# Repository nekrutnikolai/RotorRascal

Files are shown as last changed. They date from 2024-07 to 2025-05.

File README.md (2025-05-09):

## Final Project Report

<p align="center">
    Final Project Website for ECE 5730<br>
    Bryan Peters (bmp85), Martin Kostal (mk2378), Nikolai Nekrutenko (nan34)
</p>

<p align="center">
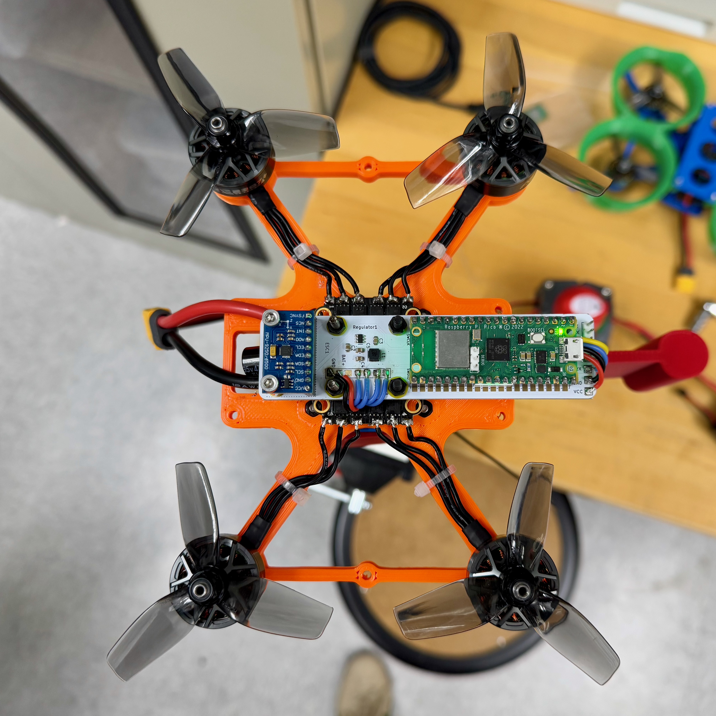
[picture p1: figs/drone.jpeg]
Drone
    
</p>

### Project Introduction

#### One sentence "sound bite" that describes your project
    
We built and implemented PID control on a Pico-powered quadcopter to hover on a gimbal stand with throttle input from a controller. 

#### A summary of what you did and why

We built a functional quadcopter system powered by a Raspberry Pi Pico, implementing a full PID-based flight controller from scratch to enable stable hover on a custom gimbal stand. Our goal was to design a hands-on, educational drone platform that could be integrated into ECE and MAE course curricula, allowing students to work directly with embedded systems, control theory, and dynamics. Starting from a partially developed hardware prototype and minimal software, we developed our own PID control logic, tuned it through extensive testing, and integrated radio-based throttle control. This project not only demonstrated our understanding of embedded flight control, but also laid the groundwork for a low-cost, reproducible drone platform for future student use.

### High level design

#### Rationale and sources of your project idea

Bryan, Martin and I enjoy drones and quadcopters, we thought it would be a neat idea to develop a somewhat functioning flight controller to control the drone with an onboard IMU for orientation data, an external remote to set the throttle position, and an electronic speed controller (ESC). 
    
Nikolai is a part of the Motion Studio "Drone Squad" advised by Dr. Beatriz Asfora which was involved in the creating of this final project idea. Out of the Drone Squad there was already a prototype developed by Deemo Chen with a PCB integrating an IMU and Pi Pico along with a skeleton of code on how to control each PWM ESC channel.

The long-term objective of this project is to support the integration of these Pico-based drones made from 3D printed components into ECE and MAE courses. For instance, these drones could be integrated in the ECE microcontrollers curriculum and the students could work on code developing/tuning a PID controller. Or, for a MAE dynamics course, the students could use these drones for dynamics modelling.

#### Background math

The effects of a $P$, $I$ and $D$ terms are well know. If we think of controlling the mass in a spring-mass-dashpot system, the $P$ term acts like increasing the stiffness of the spring, whereas the $D$ term effectively adds damping to the system. An $I$ term in general achieves the desirable property of having zero steady state. 

Even though our system is not a spring-mass-dashpot system, we can still keep in mind the above intuitive properties of each of the three terms of a PID controller. 
    
We ended up using the same set of three $P$, $I$, $D$ coefficients for controlling the pitch and the roll angle, and a different set of three $P$, $I$, $D$ coefficients for the yaw angle. Therefore, $6$ in total.

We did not do any modelling of the drone ("plant") dynamics, and did the tuning by trial and error. With more time, we would obtain the equations of motion and linearize about the desired hover position. We would get a linear set of equations, keeping in mind that we should include a model of noise in the measurements obtained from the IMU. There would be two standard approaches we could have taken: either design the controller using the state-space approach, or frequency design. Preceeding each of these two approaches, we would first have to obtain the dynamical equations of motion from Newton's second law and then linearize them about the desired hover position. 

Getting the dynamical equations of motion would have been non-trivial for several reasons, and was not achievable in the allocated time for this project. First of all, we would have to obtain the center of mass and tensor of inertia with respect to the gimbal, treating the drone as a rigid body. This could have been obtained from a CAD assembly, but only approximately - due to the geometry of $3D$ printed layers, see linked files for the individual parts. (Furthermore, the chip itself, the IMU, the wiring, the battery would all change these quantities, and indicate why it would have been really hard to obtain at least a reasonable model of the dynamics.) Second of all, the friction at the gimbal on the frame of the drone and the pull of the cables would have to be modelled. The thrust of the propellers in terms of the duty cycle of our PWM control signal supplied to the motors would be obtained from the documentation of the propeller's manufacturer. We should keep in mind that the gimbal support was not located under the center of mass. 

#### Logical structure
   
1. Initialize radio and sensors
2. Calibrate ESCs and Gyro
3. Initialize serial PID tuning interface
4. Wait for arm signal from controller
    1. Erase all store PID values -- effectively reset controls
5. Spin up motors to minimum throttle and begin executing PID loop
6. Continue executing PID loop until disarm

<p align="center">
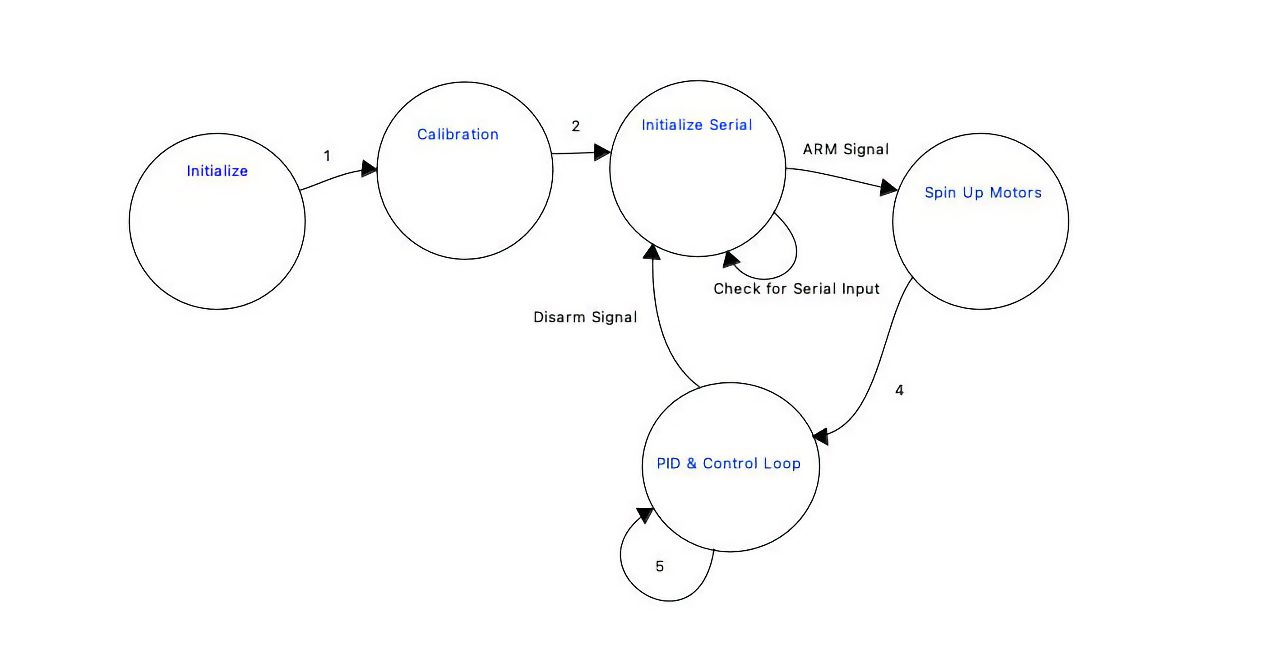
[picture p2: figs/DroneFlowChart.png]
DroneChart
    
</p>

#### Hardware/software tradeoffs
    
- **PID loop speed:** Since the drone is a complicated, unstable system with 4 motors and 6 degrees of freedom, it is vital to have a fast control loop. From our testing and with lab 3, we found a value of 1kHz to work well. Compared to lab 3, we need to be computing the PID terms for 3 axes as opposed to a single PID axis. Those three axes are pitch, roll, and yaw. Pitch and roll have the same PID parameters and yaw has different PID parameters that will be discussed later in this section. 

- **Pico W:** The Pico W was used to allow future expansion of wireless capabilities. Future work could involve developing a web server that hosts an interactive PID tuning interface where students in courses could drag sliders and visualize the gyro output and controller output to see the performance of the PID developed or the drone modelled.

- **Controlling 4 Motors:** The PWM needs to be computed for each of the 4 motors, as opposed to a single axis like in lab 3, which takes more time to compute. This point is combined with the previous point made above, leading to significantly more computation involved. Essentially, 6 (PID terms) x 3 (axes) x 4 (motors) = 64 times the amount of computation relative to lab 3 since that lab had 1 axis and 1 motor. Additionally, changing the motor output has effects on the physical system, where changing the motor speed induces a torque on the drone, affecting the yaw axis, which will be discussed in the next section.

- **Yaw Compensation:** Since the drone is a physical system, we had to take into account physics for our software development and development. The quick and dirty solution that we came up with was having different PID weights for the yaw axis as opposed to the pitch and roll axes. For instance, the D term had to be greatly reduced as so the yaw compensation would not fight the other axes and enter an unstable jittery mess.

- **Long-Term Gyro Drift:** Gyro drift could have an effect on the longer-term characteristics in the minute to hour timescales. This is not much of a concern, however, as the drone only has battery life for 5 minutes at most due to the extreme power draw of flight. We implemented the gyro to calibrate everytime a battery is plugged in, so the drone must be set level.

#### Discuss existing patents, copyrights, and trademarks which are relevant to your project.

There are no existing patents, copyrights, and trademarks which are relevant to our project.

### Program/hardware design

#### Program details. What parts were tricky to write?

The skeleton of code we started from was unnecessarily complicated, so our biggest challenge was discovering how the actual control algorithms and peripheral interfaces were implemented. The code for the radio interface was reverse-engineered based on the serial string received from the controller. Although that was straightforward, it was far less straightforward to implement pitch, roll, and yaw control from the controller to the rest of the code. Hence, we stuck with throttle and arm only. From there, we scrapped his PID control as it was unfinished and did not work and wrote our own. This has its own challenges as we are implementing it on a quadcopter with four motors. One really important thing that we realized early was that the physical model for how yaw is controlled is extremely different from how pitch and roll is controlled. This means we needed separate coefficients for yaw PID and pitch/roll PID. To implement this, we simply compute the PID values, then apply the coefficients separately in the motor mixing calculations. 

The code has the following structure:

```
RotorRascals
├── main.c                  # Entry point, initializes hardware and control loop
├── lib/
│   ├── Control/
│   │   ├── controller.c       # PID controller logic
│   │   └── controller.h
│   ├── ESC/
│   │   ├── esc.c              # Motor PWM control
│   │   └── esc.h
│   ├── Filter/
│   │   ├── leaky_LP.c         # Leaky low-pass filter
│   │   └── leaky_LP.h
│   ├── MPU9250/
│   │   ├── mpu9250.c          # IMU driver
│   │   └── mpu9250.h
│   ├── Radio/
│   │   ├── radio.c            # UART radio input parsing
│   │   └── radio.h
├── include/
│   ├── config.h               # System-wide configuration macros
│   └── pins.h                 # Pin definitions
├── utils/
│   └── math_utils.c/h         # Optional math helpers
├── Makefile or CMakeLists    # Build system configuration
```
  
#### Hardware details -- Could someone else build this based on what you have written?

Below is a diagram showcasing the drone components

<p align="center">
    DroneLabelled
</p>

The drone 3D printable files can be found at the following link:
1. DIYDrone Frame with Motor Holes:
https://cad.onshape.com/documents/d38aab018657bf04d68fdbe6/w/71b7a7a8d496a9da1491b
bbb/e/70127a797fc69afda087e221
2. DIYDrone (Jackson & Dylan) Guards:
https://cad.onshape.com/documents/7de229710a5769dcea70d33f/w/a361731c2e298d2c6e283
035/e/6aab78923736995bb8b96cf8
3. DIYDrone Gimbal Interfacer:
https://cad.onshape.com/documents/8b853f430eb67b22ed155352/w/298f6506e82bca0de68ad
df6/e/2c12097c2bd1bacce00dfebb?renderMode=0&uiState=680d8b0e72d068090b086e62
4. Drone Gimbal Mount & Gimbal Drone Spacer:
https://cad.onshape.com/documents/e9f49230253cb2ceb026b522/w/5f775122fa42329de5afc46
6/e/d2d7e1e364a8d0e3d6eb7b74

The drone build guide can be found at the following links:
1. Frame 3D printing guide: https://github.com/cornellmotionstudio/DIYDrone/wiki/Frame
2. Guards 3D priting guide: https://github.com/cornellmotionstudio/DIYDrone/wiki/Guards
3. Mechanical assembly guide: https://github.com/cornellmotionstudio/QuadPopUp/wiki/Part-1:-Build-Your-Quadcopter 
4. Electrical assembly/Pico software guide: https://github.com/cornellmotionstudio/JacksonDronev2/wiki

To get up and running with the code and Pico build environment:

Clone the project
``` bash
git clone https://github.com/nekrutnikolai/RotorRascal.git
```

Go to the software dir.
``` bash
cd RotorRascal && cd software
```

Build the project
``` bash
./builder
```

Below is a bill of materials will all the parts necessary to build the drone and get up and running

Table 1: Drone components

| **Component** | **Part Description** | **Estimated Price** |
|---|---|---|
| **Frame** | 3D Printed | $3-5 in filament |
| **Motors** | 2306 brushless motors, 1700–2500KV | $15–$30 each |
| **ESC (4-in-1)** | 4-in-1 ESC, 30–60A, DShot600 support | $40–$80 |
| **Propellers** | 3" tri-blade props | $3–$6 per set |
| **Radio Receiver (Rx)**| ELRS protocol receiver | $15–$30 |
| **Battery** | 4S LiPo, 1300–1800mAh | $25–$50 |

Table 2: Drone accessories

| **Component** | **Part Description** | **Estimated Price** |
|---|---|---|
| **Transmitter (Tx)** | Radiomaster Boxer ELRS RC controller | $100–$150 |
| **Battery Charger** | LiPo balance charger (AC/DC or DC only) | $40–$100 |

#### Be sure to specifically reference any design or code you used from someone else
    
We referenced the design and code found at the following repository: https://github.com/cornellmotionstudio/JacksonDronev2

### Tuning the drone PID's

Tuning the PIDs on a quadcopter is not the easiest task when it comes to a PID loop that you wrote yourself, on hardware that you also built yourself. It's especially difficult because there is no advice from other people that have experienced the issues. It boils down to a raw understanding of the physical model and the code at play. With our particular situation, the most difficult thing was trying to understand what was due to the gyro or if the issues were being caused by dynamics between the pitch and roll competing with yaw correction. Due to the physical model of a quadcopter, if a correction is made to any motor, it affects yaw, therefore inducing a yaw error that requires correction. Finding a starting point that did not have an oscillatory loop between the pitch/roll axis and the yaw axis was a challenge, but in the end, we were able to find a good starting point PIDs.

Table 3: Initial PID values

| Axis | Kp  | Ki | Kd |
|---|-----|---|---|
| Roll/Pitch  | 4.5 | 0.4  | 0.08  |
| Yaw | 3.0 | 0.25 | 0.015 |

Continuing with our tuning, we were able to find really good PID values that resulted in an ability to react really well to outside stimuli, hold level quite well, and correct for new changes in center of gravity on the drone. The biggest challenge is finding a set of PIDs that works well through the whole throttle range; however, though this should not be the case unless we are amplifying noise or vibration caused by different throttle positions in our accelerometer measurements. Something we did still experience regardless of the amount of tuning done was a continuous angle error that varied with time; it almost appeared to be steady-state error that would then be corrected by the I term, which led us down some tuning rabbit holes in attempts to fix it. However, we believe now that it is actually drift occurring through our complimentary filter, and given more time, I believe we would have been able to correct this issue. Coming to this conclusion was based on testing with a solid offset that would need to be corrected by the I term, which did occur and namely occurred much faster than the correction to this drift. Additionally, testing our P term by tapping different points to induce an angle error and observing how quickly the drone corrected these errors indicated that whatever this drift was, it was being ignored by the PID loop. Testing PIDs was done purely on a custom-designed stand designed by Nikolai. The stand allows the drone to move along the pitch, roll, yaw, and vertical axis. Meaning we can simulate a hover that is restricted in translational movement. Using this stand with a power cable and a USB cable dangling from opposite ends of the drone, we are able to safely test indoors despite the high chance of unstable flight. 

Table 4: Final PID values that we found to work best:

| Axis | Kp  | Ki | Kd |
|---|-----|---|---|
| Roll/Pitch  | 20.0 | 2.0  | 1.5  |
| Yaw | 3.0 | 0.25 | 0.015 |

### Results of the design

#### Any and all test data, scope traces, waveforms, etc

We tested the drone primarily on a custom-designed gimbal stand, which allowed safe experimentation of all rotational degrees of freedom (roll, pitch, yaw) and limited vertical movement. This setup enabled us to analyze hover stability, responsiveness, and overall system behavior under controlled conditions.

We evaluated PID response by:
- Applying known disturbances (e.g., tapping the frame) and observing response.
- Introducing sudden changes in throttle and analyzing recovery behavior.
- Monitoring gyro outputs in real time via serial logging.

Through this process, we fine-tuned the PID constants as shown in Table 4. 

Unfortunately, due to the 1kHz speed of the PID loop, we were unable to plot the data in real time without a noticeable reduction in performance.

#### Speed of execution (hesitation, flicker, interactiveness, concurrency)

The control loop was executed at **1 kHz**, which allowed timely updates and stable feedback. This speed was chosen based on earlier experimentation and provided a good balance between performance and computational headroom on the Pi Pico. There was **no observable hesitation or lag**, and the drone maintained high responsiveness to throttle changes and physical disturbances.

#### Accuracy (numeric, music frequencies, video signal timing, etc)

The orientation estimation was reasonably accurate for short time scales (under 2–3 minutes), with minor long-term drift observed due to IMU noise and limitations of the complementary filter. Control accuracy was sufficient to maintain a level hover and reject disturbances, though we noticed yaw compensation would lag slightly under certain conditions due to cross-axis coupling as a result of torque induced by the drone.

#### How you enforced safety in the design

Safety was a top priority throughout this project. The following measures were implemented:

- Test stand: Limited movement to safe ranges while enabling realistic control behavior.
- Throttle arm/disarm mechanism: Prevents accidental motor spin-up.
- Motor failsafe: If communication is lost, motors shut down immediately.
- Battery-powered only during flight: USB only used for debugging and PID tuning on the stand.
- PID zeroing on arm: Ensures no accumulated integral error before startup and prevents loss of fingers.
- Frame guards (optional): Optional frame propeller guards can be 3D printed and built into the frame 

These precautions allowed extensive indoor testing without risk to people or equipment.

#### Usability by you and other people

Our system was used by all group members and debugged collaboratively. Some key usability points include:

- Builder script simplified firmware compilation and flashing.
- Serial PID tuner allowed real-time adjustments, improving iteration speed.
- Open-source hardware/software make this project replicable by other students, especially within ECE/MAE courses.
- Documentation and GitHub Wiki were created to support further student use and integration.

### Conclusion

#### Analyse your design in terms of how the results met your expectations. What might you do differently next time?

Given more time, after a thorough analysis outlined in the section "background method", we would obtain the equations of motion and proceed to linearize them about the desired hover position. These would then guide us in our tuning process, by suggesting ranges of values for which the controller gains would result in a stable hovering equilibirum. In particular, the MATLAB controls toolbox would likely be vital in this process. We would then iterate over a loop of trial and tuning, until we obtain the desired response characteristics.   

#### How did your design conform to the applicable standards?

Our design aligns with several widely recognized engineering and safety standards:
- IEEE 21451: Our use of digital communication with the IMU and radio receiver follows the principles of this standard, which defines smart transducer interfaces for sensors and actuators. This is especially relevant to our modular use of sensors and potential expansion via Wi-Fi on the Pico W.
- IEEE 829 (Test Documentation Standard): While not formalized, we structured our testing methodology (PID tuning, safety checks, failure recovery) based on the principles of repeatable test planning and documentation.
- FCC Part 15: The 2.4 GHz radio communication between the transmitter and ELRS receiver operates in compliance with unlicensed ISM band regulations. Our system is entirely self-contained and avoids intentional emissions outside allowed frequencies.
- ISO 12100 (Safety of Machinery - Risk Assessment): We applied the principles of this standard by implementing startup gyro calibration, arm/disarm logic, and motor cutoff on communication loss. Testing on a gimbal stand further reduced risk during development.
- ISO 9001 (Quality Management): Though not formally certified, we adhered to quality principles including version-controlled development, structured documentation, and modular hardware/software integration to ensure maintainability and reproducibility for future coursework.

#### Intellectual property considerations

- **Did you reuse code or someone else's design?**
    Yes, we built up on top of code and hardware developed by the Motion Studio Drone Squad and Deemo Chen.

    The code and hardware that we built on top of can be found at the following GitHub repositories:
    - https://github.com/cornellmotionstudio/QuadPopUp
    - https://github.com/cornellmotionstudio/DIYDrone
    - https://github.com/cornellmotionstudio/JacksonDronev2
    
- **Did you use code in the public domain?**

    Yes, the Motion Studio GitHub repositories found above are public. 

- **Are you reverse-engineering a design? How did you deal with patent/trademark issues?**

    N/A, we are not reverse-engineering a design.

- **Did you have to sign non-disclosure to get a sample part?**

    No, we did not have to sign an NDA.

- **Are there patent opportunities for your project?**

    There are not patent opportunities for our project as most of this has already been dveloped and is available commerically.

### Appendix A (permissions)

The group ***approves*** this report for inclusion on the course website.

The group ***approves*** the video for inclusion on the course youtube channel.

### Additional appendices

- **Appendix with commented Verilog and/or program listings.**

Our commented code can be found at the following link in our repository: https://github.com/nekrutnikolai/RotorRascal/tree/master/software

- **Appendix with schematics if you build hardware external to the DE1-SoC board (you can download free software from expresspcb.com to draw schematics).**

<p align="center">
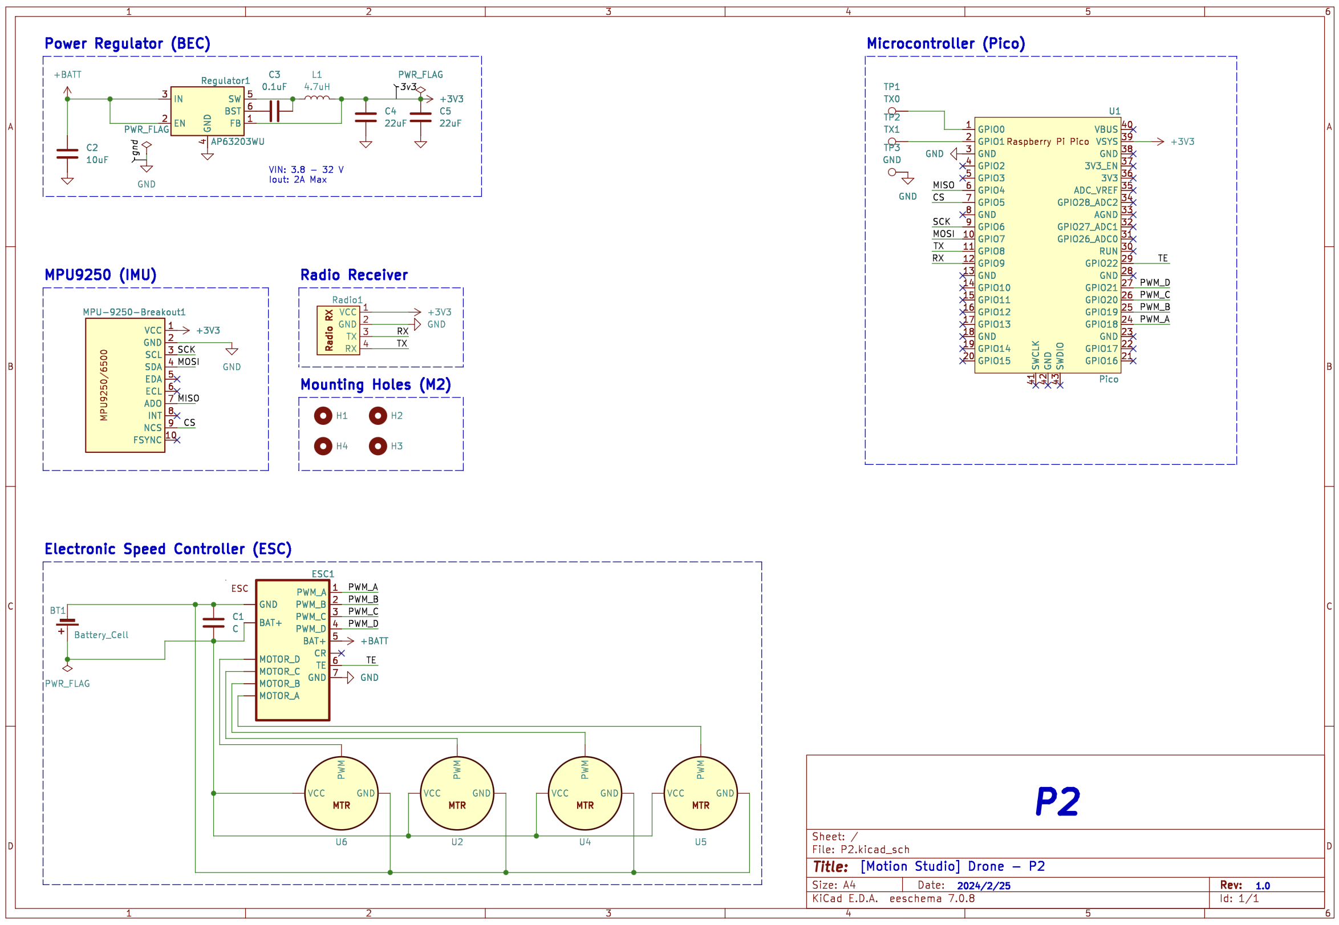
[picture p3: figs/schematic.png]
DroneSchematic
    
</p>

- **Appendix with a list of the specific tasks in the project carried out by each team member.**

    A list specific tasks is not appropriate for this project because we worked together on everything as a team. As a result, the contribution of each team is split roughly evenly.

- **References you used:**

    - Yaw compensation as implemented in BetaFlight (the most popular hobbyist flight software): https://betaflight.com/docs/wiki/guides/current/integrated-yaw
    - BetaFlight suggested tuning principles: https://betaflight.com/docs/wiki/guides/current/Freestyle-Tuning-Principles#suggested-setting-values-for-a-5-5

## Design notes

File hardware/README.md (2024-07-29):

# Schematics
KiCad Schematics

*Note: please export the schematics to `P2.svg` so this README can preview it correctly*

The controller software can be found here: https://github.com/MotionStudioCornell/P2

P2-Schematics

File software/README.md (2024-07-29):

# P2 Flight Controller

Custom Pico-based flight controller/computer software.

The KiCad Schematics can be found here: https://github.com/MotionStudioCornell/P2-Schematics

## Dev Info

### MPU9250
Data Sheet: https://invensense.tdk.com/wp-content/uploads/2015/02/PS-MPU-9250A-01-v1.1.pdf

Register Map: https://invensense.tdk.com/wp-content/uploads/2015/02/MPU-9250-Register-Map.pdf

### Pi Pico(W)
Documents: https://www.raspberrypi.com/documentation/microcontrollers/c_sdk.html

## Build

Requirement:

Raspberry Pi Pico C/C++ SDK

`cd build`

`cmake ../src -DPICO_BOARD=pico_w`

`make`

## Flash

Find `P2.uf2` in the `build` folder, and drag it onto the Pico MSD(Or any methods you prefer)

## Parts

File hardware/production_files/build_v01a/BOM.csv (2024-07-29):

Designator | Footprint | Comment
C3 | C_0805_2012Metric | 0.1uF
C2 | C_0805_2012Metric | 10uF
L1 | L_Abracon_ASPI-4030S | 4.7uH
Regulator1 | TSOT-23-6 | AP63203WU
C4,C5 | C_0805_2012Metric | 22uF

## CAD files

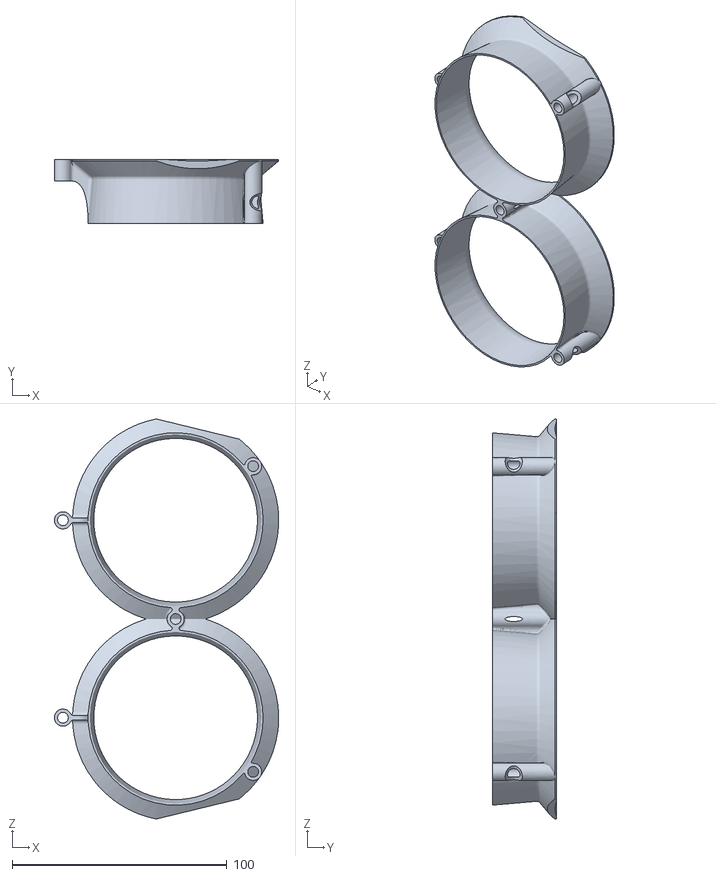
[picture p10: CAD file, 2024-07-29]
frame/guard.stl
104.5 x 30.0 x 186.3

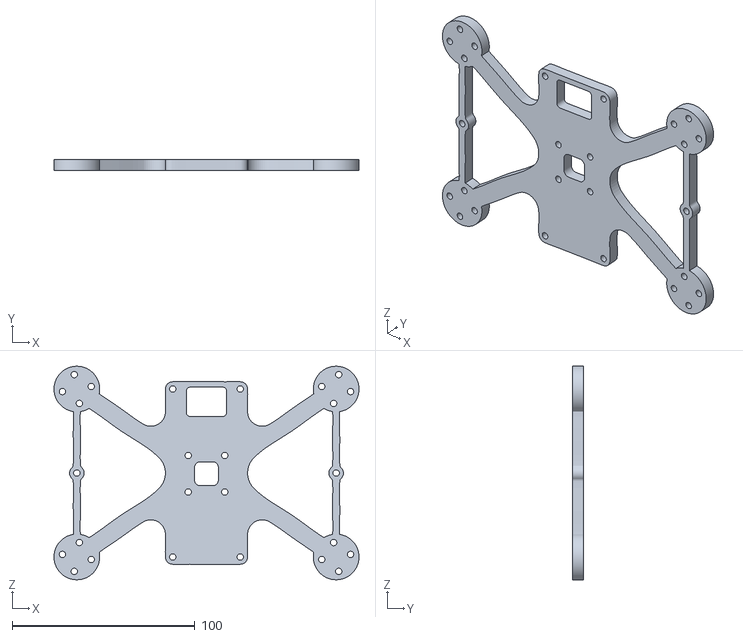
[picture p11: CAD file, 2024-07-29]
frame/buttom-plate.stl
167.0 x 6.00 x 116.9

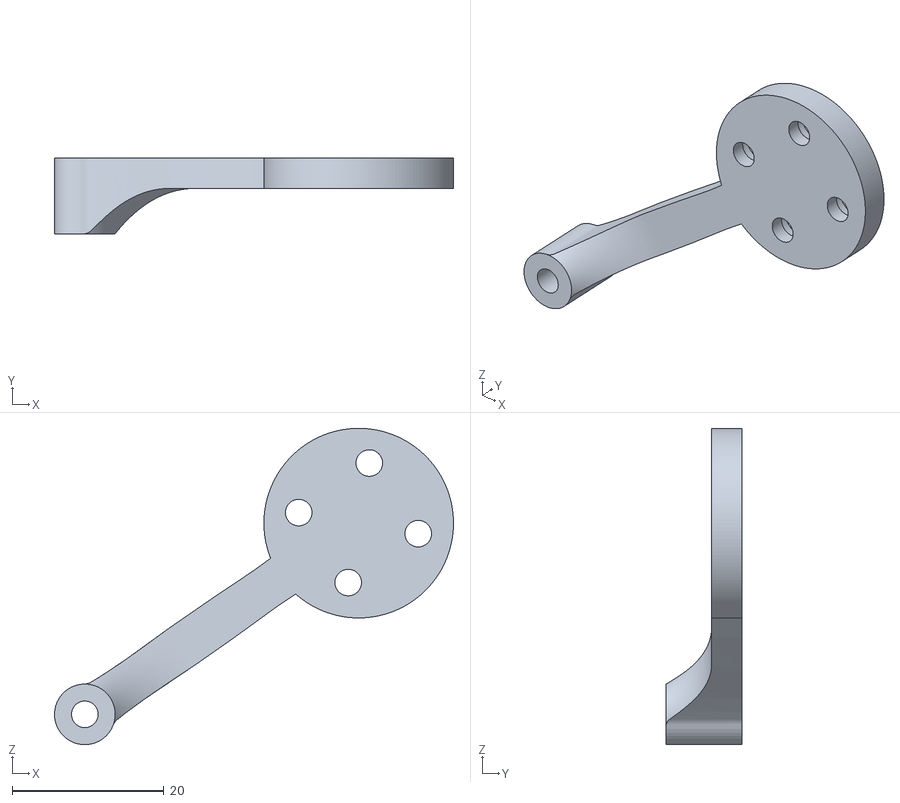
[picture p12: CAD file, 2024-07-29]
frame/gurad-extend.stl
52.6 x 10.0 x 41.7

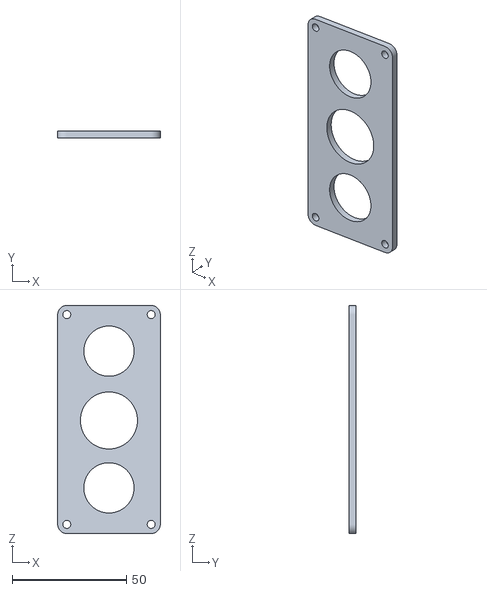
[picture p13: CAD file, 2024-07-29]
frame/top-plate.stl
45.0 x 3.00 x 99.9

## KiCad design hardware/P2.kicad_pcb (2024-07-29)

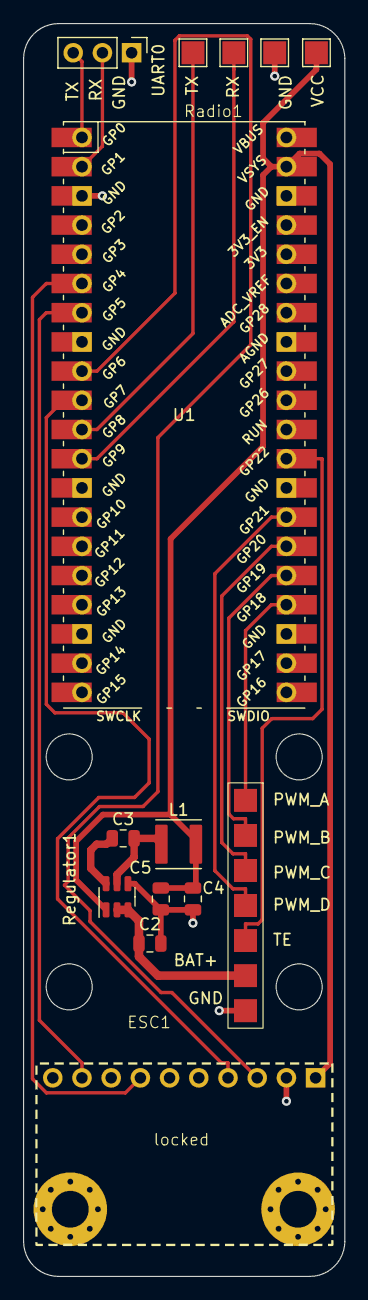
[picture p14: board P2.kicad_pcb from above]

Board: 2 copper layers, 27.9 x 109.0 mm, 17 parts (0 on the bottom side), 18 nets.

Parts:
C2: 10uF; C_0805_2012Metric
C3: 0.1uF; C_0805_2012Metric
C4, C5: 22uF; C_0805_2012Metric
ESC1: ESC
H1, H2, H3, H4: MountingHole; MountingHole_4mm
H5, H6: MountingHole; MountingHole_3.2mm_M3_Pad_Via
L1: 4.7uH; L_Abracon_ASPI-4030S
Radio1: Radio
Regulator1: AP63203WU; TSOT-23-6
U1: Pico; RPi_Pico_SMD_TH
UART0: UART; PinHeader_1x03_P2.54mm_Vertical
locked: MPU9250-Breakout

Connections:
+3V3: C4.1, C5.1, L1.2, Radio1.1 (VCC), Regulator1.1 (FB), U1.39 (VSYS), locked.1 (VCC)
+BATT: C2.1, ESC1.5 (BAT+), Regulator1.2 (EN), Regulator1.3 (IN)
/CS: U1.7 (GPIO5), locked.9 (NCS)
/MISO: U1.6 (GPIO4), locked.7 (ADO)
/MOSI: U1.10 (GPIO7), locked.4 (SDA)
/PWM_A: ESC1.1 (PWM_A), U1.24 (GPIO18)
/PWM_B: ESC1.2 (PWM_B), U1.25 (GPIO19)
/PWM_C: ESC1.3 (PWM_C), U1.26 (GPIO20)
/PWM_D: ESC1.4 (PWM_D), U1.27 (GPIO21)
/RX: Radio1.3 (TX), U1.12 (GPIO9)
/SCK: U1.9 (GPIO6), locked.3 (SCL)
/TE: ESC1.6 (TE), U1.29 (GPIO22)
/TX: Radio1.4 (RX), U1.11 (GPIO8)
GND: C2.2, C4.2, C5.2, ESC1.7 (GND), Radio1.2 (GND), Regulator1.4 (GND), U1.3 (GND), UART0.1, locked.2 (GND)
unnamed: U1.2 (GPIO1), UART0.2
unnamed: U1.1 (GPIO0), UART0.3
unnamed: C3.1, Regulator1.6 (BST)
unnamed: C3.2, L1.1, Regulator1.5 (SW)

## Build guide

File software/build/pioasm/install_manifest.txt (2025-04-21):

/Users/nekrutnikolai/git/RotorRascal/software/build/pioasm-install/pioasm/pioasm
/Users/nekrutnikolai/git/RotorRascal/software/build/pioasm-install/pioasm/pioasmTargets.cmake
/Users/nekrutnikolai/git/RotorRascal/software/build/pioasm-install/pioasm/pioasmTargets-release.cmake
/Users/nekrutnikolai/git/RotorRascal/software/build/pioasm-install/pioasm/pioasmConfig.cmake
/Users/nekrutnikolai/git/RotorRascal/software/build/pioasm-install/pioasm/pioasmConfigVersion.cmake

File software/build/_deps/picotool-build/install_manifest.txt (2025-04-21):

/Users/nekrutnikolai/git/RotorRascal/software/build/_deps/picotool/picotool
/Users/nekrutnikolai/git/RotorRascal/software/build/_deps/picotool/picotoolTargets.cmake
/Users/nekrutnikolai/git/RotorRascal/software/build/_deps/picotool/picotoolTargets-release.cmake
/Users/nekrutnikolai/git/RotorRascal/software/build/_deps/picotool/picotoolConfig.cmake
/Users/nekrutnikolai/git/RotorRascal/software/build/_deps/picotool/picotoolConfigVersion.cmake

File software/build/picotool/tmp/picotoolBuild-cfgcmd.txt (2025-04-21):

cmd='/opt/homebrew/bin/cmake;--no-warn-unused-cli;-DCMAKE_MAKE_PROGRAM:FILEPATH=/usr/bin/make;-DPICO_SDK_PATH:FILEPATH=/Users/nekrutnikolai/git/pico-sdk;-DPICOTOOL_NO_LIBUSB=1;-DPICOTOOL_FLAT_INSTALL=1;-DCMAKE_INSTALL_PREFIX=/Users/nekrutnikolai/git/RotorRascal/software/build/_deps;-DCMAKE_RULE_MESSAGES=OFF;-DCMAKE_INSTALL_MESSAGE=NEVER;-GUnix Makefiles;-S;<SOURCE_DIR><SOURCE_SUBDIR>;-B;<BINARY_DIR>'

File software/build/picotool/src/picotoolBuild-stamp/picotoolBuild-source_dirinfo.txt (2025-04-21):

# This is a generated file and its contents are an internal implementation detail.
# The download step will be re-executed if anything in this file changes.
# No other meaning or use of this file is supported.

method=source_dir
command=
source_dir=/Users/nekrutnikolai/git/RotorRascal/software/build/_deps/picotool-src
work_dir=

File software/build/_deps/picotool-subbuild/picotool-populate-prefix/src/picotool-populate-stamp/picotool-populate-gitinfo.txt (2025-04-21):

# This is a generated file and its contents are an internal implementation detail.
# The download step will be re-executed if anything in this file changes.
# No other meaning or use of this file is supported.

method=git
command=/opt/homebrew/bin/cmake;-DCMAKE_MESSAGE_LOG_LEVEL=VERBOSE;-P;/Users/nekrutnikolai/git/RotorRascal/software/build/_deps/picotool-subbuild/picotool-populate-prefix/tmp/picotool-populate-gitclone.cmake
source_dir=/Users/nekrutnikolai/git/RotorRascal/software/build/_deps/picotool-src
work_dir=/Users/nekrutnikolai/git/RotorRascal/software/build/_deps
repository=https://github.com/raspberrypi/picotool.git
remote=origin
init_submodules=TRUE
recurse_submodules=--recursive
submodules=
CMP0097=NEW

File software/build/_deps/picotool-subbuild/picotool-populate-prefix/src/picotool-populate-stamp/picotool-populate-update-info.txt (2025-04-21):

# This is a generated file and its contents are an internal implementation detail.
# The patch step will be re-executed if anything in this file changes.
# No other meaning or use of this file is supported.

command (connected)=/opt/homebrew/bin/cmake;-Dcan_fetch=YES;-DCMAKE_MESSAGE_LOG_LEVEL=VERBOSE;-P;/Users/nekrutnikolai/git/RotorRascal/software/build/_deps/picotool-subbuild/picotool-populate-prefix/tmp/picotool-populate-gitupdate.cmake
command (disconnected)=/opt/homebrew/bin/cmake;-Dcan_fetch=NO;-DCMAKE_MESSAGE_LOG_LEVEL=VERBOSE;-P;/Users/nekrutnikolai/git/RotorRascal/software/build/_deps/picotool-subbuild/picotool-populate-prefix/tmp/picotool-populate-gitupdate.cmake
work_dir=/Users/nekrutnikolai/git/RotorRascal/software/build/_deps/picotool-src

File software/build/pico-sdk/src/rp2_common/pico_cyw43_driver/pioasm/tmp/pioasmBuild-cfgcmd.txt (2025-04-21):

cmd='/opt/homebrew/bin/cmake;--no-warn-unused-cli;-DCMAKE_MAKE_PROGRAM:FILEPATH=/usr/bin/make;-DPIOASM_FLAT_INSTALL=1;-DCMAKE_INSTALL_PREFIX=/Users/nekrutnikolai/git/RotorRascal/software/build/pioasm-install;-DCMAKE_RULE_MESSAGES=OFF;-DCMAKE_INSTALL_MESSAGE=NEVER;-GUnix Makefiles;-C<TMP_DIR>/pioasmBuild-cache-$<CONFIG>.cmake;-S;<SOURCE_DIR><SOURCE_SUBDIR>;-B;<BINARY_DIR>'

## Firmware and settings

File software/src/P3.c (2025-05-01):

#include <stdio.h>
#include <stdlib.h>
#include "pico/stdlib.h"
#include "hardware/spi.h"
#include "hardware/pwm.h"
#include "hardware/uart.h"
#include "hardware/irq.h"
#include "hardware/flash.h"
#include "pico/binary_info.h"
#include "pico/critical_section.h"
#include "../lib/MPU9250/mpu9250.h"
#include "../lib/ESC/esc.h"
#include "../lib/Filter/leaky_LP.h"
#include "../lib/Control/controller.h"
#include "../lib/Radio/radio.h"
#include "pico/cyw43_arch.h"
#include <math.h>
#include <time.h>

#define PIN_MISO 4
#define PIN_CS 5
#define PIN_SCK 6
#define PIN_MOSI 7

#define PWM_WRAP 100000
#define PWM_FREQ 50
#define MAX_DUTY 0.1
#define MIN_DUTY 0.05
#define PIN_PWM1 21
#define PIN_PWM2 20
#define PIN_PWM3 19
#define PIN_PWM4 18

#define RADIO_TX 8
#define RADIO_RX 9

#define Default_Kp 20
#define Default_Ki 2
#define Default_Kd 1.5
#define Default_yaw_Kp 0
#define Default_yaw_Ki 0
#define Default_yaw_Kd 0

#define INIT_THROTTLE 5.0

#define dT_ms 1
#define dT_s (dT_ms / 1000.0)

#define FLASH_TARGET_OFFSET (PICO_FLASH_SIZE_BYTES - 4096)
#define VALID_MARKER 0xDEADBEEF

static mpu9250 imu;
static ESC esc;
static leaky_lp w_filter;
static leaky_lp a_filter;
static controller fc;
static radio rdo;

const uint8_t *flash_target_contents = (const uint8_t *)(XIP_BASE + FLASH_TARGET_OFFSET);

typedef struct {
    float kp, ki, kd;
    float kp_yaw, ki_yaw, kd_yaw;
    uint32_t marker;
} pid_storage_t;

void read_pid_values(controller *fc) {
    const pid_storage_t *stored = (const pid_storage_t *)flash_target_contents;
    if (stored->marker == VALID_MARKER) {
        fc->Kp = stored->kp;
        fc->Ki = stored->ki;
        fc->Kd = stored->kd;
        fc->Kp_yaw = stored->kp_yaw;
        fc->Ki_yaw = stored->ki_yaw;
        fc->Kd_yaw = stored->kd_yaw;
    }
}

void write_pid_values(const controller *fc) {
    uint8_t buffer[4096];
    memcpy(buffer, flash_target_contents, 4096);
    pid_storage_t *stored = (pid_storage_t *)buffer;

    stored->kp = fc->Kp;
    stored->ki = fc->Ki;
    stored->kd = fc->Kd;
    stored->kp_yaw = fc->Kp_yaw;
    stored->ki_yaw = fc->Ki_yaw;
    stored->kd_yaw = fc->Kd_yaw;
    stored->marker = VALID_MARKER;

    uint32_t ints = save_and_disable_interrupts();
    flash_range_erase(FLASH_TARGET_OFFSET, 4096);
    flash_range_program(FLASH_TARGET_OFFSET, buffer, 4096);
    restore_interrupts(ints);
}

volatile bool new_input = false;
char serial_buffer[64];
int serial_buffer_index = 0;

void print_pid_values() {
    printf("Current PID values:\n");
    printf("Kp = %.3f, Ki = %.3f, Kd = %.3f\n", fc.Kp, fc.Ki, fc.Kd);
    printf("Kp_yaw = %.3f, Ki_yaw = %.3f, Kd_yaw = %.3f\n", fc.Kp_yaw, fc.Ki_yaw, fc.Kd_yaw);
}

void handle_serial_input() {
    int c;
    while ((c = getchar_timeout_us(0)) != PICO_ERROR_TIMEOUT) {
        if (c == '\n' || c == '\r') {
            if (serial_buffer_index > 0) {
                serial_buffer[serial_buffer_index] = '\0';

                if (strncmp(serial_buffer, "kp=", 3) == 0) {
                    fc.Kp = atof(serial_buffer + 3);
                } else if (strncmp(serial_buffer, "ki=", 3) == 0) {
                    fc.Ki = atof(serial_buffer + 3);
                } else if (strncmp(serial_buffer, "kd=", 3) == 0) {
                    fc.Kd = atof(serial_buffer + 3);
                } else if (strncmp(serial_buffer, "kp_yaw=", 7) == 0) {
                    fc.Kp_yaw = atof(serial_buffer + 7);
                } else if (strncmp(serial_buffer, "ki_yaw=", 7) == 0) {
                    fc.Ki_yaw = atof(serial_buffer + 7);
                } else if (strncmp(serial_buffer, "kd_yaw=", 7) == 0) {
                    fc.Kd_yaw = atof(serial_buffer + 7);
                } else {
                    printf("Invalid command. Use 'kp=<value>' or similar.\n");
                }

                write_pid_values(&fc);
                print_pid_values();
                serial_buffer_index = 0;
                new_input = true;
            }
        } else {
            if (serial_buffer_index < sizeof(serial_buffer) - 1) {
                serial_buffer[serial_buffer_index++] = (char)c;
            }
        }
    }
}

int main() {
    stdio_init_all();
    sleep_ms(2000);

    radio_setup(&rdo, RADIO_RX, RADIO_TX);
    mpu9250_setup(&imu, PIN_CS, PIN_MISO, PIN_SCK, PIN_MOSI);
    printf("Calibrating Gyro....Keep it Still...\n");
    gyro_cal(&imu, 50);
    acc_cal(&imu, 50);
    printf("Done. Offsets: w_x: %.5f, w_y:%.5f, w_z:%.5f\n", imu.w_offsets[0], imu.w_offsets[1], imu.w_offsets[2]);

    uint32_t PWM_PIN[4] = {PIN_PWM1, PIN_PWM2, PIN_PWM3, PIN_PWM4};
    esc_setup(&esc, PWM_PIN, PWM_FREQ, PWM_WRAP, MIN_DUTY, MAX_DUTY);

    printf("Calibrating ESC...\n");
    cali_motor(&esc);
    printf("Done.\n");
    printf("Arming ESC...\n");
    arm_motor(&esc);
    printf("Done.\n");

    // leaky_init(&w_filter, 0.9f);
    // leaky_init(&a_filter, 0.9f);
    // init_controller(&fc, 0.99f, dT_s, Default_Kp, Default_Ki, Default_Kd, Default_yaw_Kp, Default_yaw_Ki, Default_yaw_Kd);

    leaky_init(&w_filter, 0.9f);
    leaky_init(&a_filter, 0.9f);
    init_controller(&fc, 0.99f, dT_s, Default_Kp, Default_Ki, Default_Kd, Default_yaw_Kp, Default_yaw_Ki, Default_yaw_Kd);

    read_pid_values(&fc);

    if (cyw43_arch_init()) {
        printf("Wi-Fi init failed\n");
        return -1;
    }
    cyw43_arch_gpio_put(CYW43_WL_GPIO_LED_PIN, 1);
    sleep_ms(100);
    cyw43_arch_gpio_put(CYW43_WL_GPIO_LED_PIN, 0);
    sleep_ms(100);
    cyw43_arch_gpio_put(CYW43_WL_GPIO_LED_PIN, 1);

    while (1) {
        absolute_time_t startTime = get_absolute_time();

        handle_serial_input();

        mpu9250_update(&imu);
        float wf[3], af[3];
        leaky_update(&w_filter, imu.w, wf);
        leaky_update(&a_filter, imu.a, af);

        update_controller(&fc, wf, af);

        if (new_input) {
            new_input = false;
            printf("roll: %.3f, pitch: %.3f, yaw: %.3f\n", fc.x.roll, fc.x.pitch, fc.x.yaw);
            printf("Kp = %.3f, Ki = %.3f, Kd = %.3f, throttle = %.3f, %s\n", fc.Kp, fc.Ki, fc.Kd, rdo.throttle, rdo.controller_armed ? "ARMed" : "NOT-ARMed");
        }
        if(!rdo.controller_armed) {
            fc.integral_error.roll = 0.0f; // Reset integral error when disarmed
            fc.integral_error.pitch = 0.0f; // Reset integral error when disarmed
            fc.integral_error.yaw = 0.0f; // Reset integral error when disarmed
        }
        if (rdo.controller_armed) {
            float base_throttle = INIT_THROTTLE + rdo.throttle * ((100.0 - INIT_THROTTLE) / 100.0);

            float motor1_throttle = saturate(base_throttle + fc.u.t1 / 10.0, INIT_THROTTLE, 100.0);
            float motor2_throttle = saturate(base_throttle + fc.u.t2 / 10.0, INIT_THROTTLE, 100.0);
            float motor3_throttle = saturate(base_throttle + fc.u.t3 / 10.0, INIT_THROTTLE, 100.0);
            float motor4_throttle = saturate(base_throttle + fc.u.t4 / 10.0, INIT_THROTTLE, 100.0);

            motor_control(&esc, motor1_throttle, 1);
            motor_control(&esc, motor2_throttle, 2);
            motor_control(&esc, motor3_throttle, 3);
            motor_control(&esc, motor4_throttle, 4);
        } else {
            motor_control(&esc, 0, 1);
            motor_control(&esc, 0, 2);
            motor_control(&esc, 0, 3);
            motor_control(&esc, 0, 4);
        }

        absolute_time_t endTime = get_absolute_time();
        int64_t time_diff_ms = absolute_time_diff_us(startTime, endTime) / 1000;
        uint32_t sleep_time_ms = dT_ms > time_diff_ms ? (dT_ms - time_diff_ms) : 0;
        sleep_ms(sleep_time_ms);
    }
}

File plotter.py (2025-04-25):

#!/usr/bin/env python3

import serial
import matplotlib.pyplot as plt
import matplotlib.animation as animation
from collections import deque
import re

# Serial config
PORT = '/dev/tty.usbmodem13101'  # Change this!
BAUDRATE = 115200
MAX_POINTS = 250

# Setup regex
pattern = re.compile(r"wx:(.*?), wy:(.*?), wz:(.*?), wxf:(.*?), wyf:(.*?), wzf:(.*?), ax:(.*?), ay:(.*?), az:(.*?), axf:(.*?), ayf:(.*?), azf:(.*?)\s*$")

# Initialize data storage
fields = ['wx', 'wy', 'wz', 'wxf', 'wyf', 'wzf', 'ax', 'ay', 'az', 'axf', 'ayf', 'azf']
data = {key: deque([0.0]*MAX_POINTS, maxlen=MAX_POINTS) for key in fields}
t = deque([0]*MAX_POINTS, maxlen=MAX_POINTS)

# Setup plot
fig, ax = plt.subplots()
lines = {key: ax.plot([], [], label=key)[0] for key in fields}
ax.set_xlim(0, MAX_POINTS)
ax.set_ylim(-10, 10)
ax.legend(loc='upper left')
ax.set_title("IMU Live Stream")

# Open serial port
ser = serial.Serial(PORT, BAUDRATE, timeout=1)

def update(frame):
    global t
    try:
        line = ser.readline().decode().strip()
        match = pattern.match(line)
        if match:
            values = list(map(float, match.groups()))
            for key, val in zip(fields, values):
                data[key].append(val)
            t.append(t[-1] + 1)
            for key in fields:
                lines[key].set_data(range(len(t)), data[key])
            ax.set_xlim(max(0, len(t) - MAX_POINTS), len(t))
    except Exception as e:
        print("Parse error:", e)
    return list(lines.values())

ani = animation.FuncAnimation(fig, update, interval=50)
plt.show()

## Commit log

2024-07-29 Jackson Wiki for Edits
    [BOM.csv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]
2025-04-25 got PID working
2025-04-25 added serial PID tuning capability
2025-04-28 added yaw tuning
2025-04-30 fixed yaw directions, added controller accumulation, etc
    [P3.c]
2025-05-09 Update README.md
    Added starting PID values
